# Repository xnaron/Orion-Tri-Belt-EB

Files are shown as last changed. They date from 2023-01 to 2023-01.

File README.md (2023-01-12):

# Orion Tri-Belt-EB

This is a fork of the awesome Orion bythorsthunder.  I wanted the electronics on the bottom.  

Changed CAD is in the EB-Mod folder.  I haven't exported any stl's.

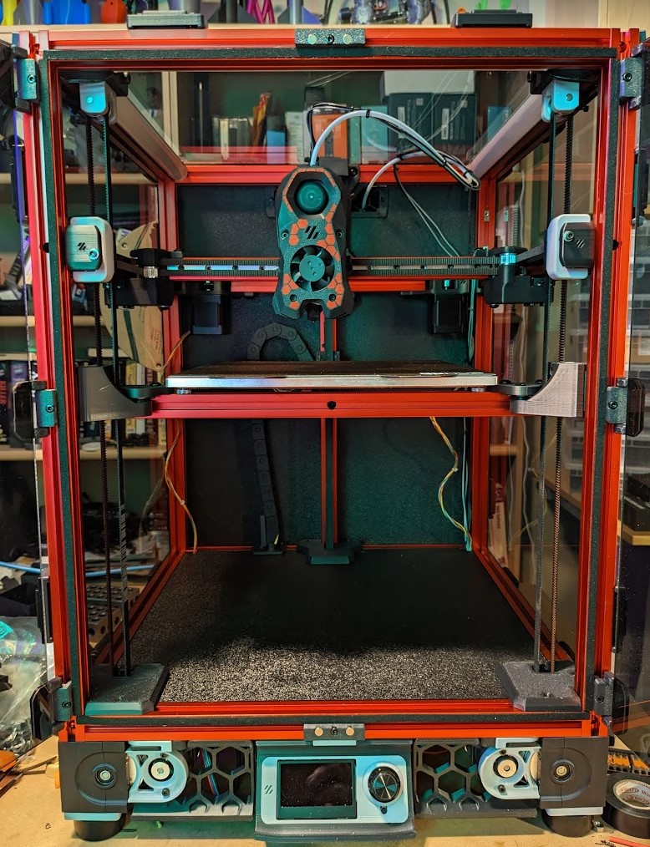
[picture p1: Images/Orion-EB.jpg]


A mod of the Voron Trident that replaces the 3 leadscrews with belts and modified Z-Drives from a 2.4.  This is in the very early stages of development and though a fully-functional printer has been built, some of the parts are not yet fully tested.  The existing printer is producing excellent prints, though many changes will be coming in the following months.

This first version places the Low Voltage Electronics up top, though I do hope to create a version in the future which is more closely matched to a stock Trident Build.  The second version will have the Z drives and low voltage electronics located on the bottom, same as in a standard Voron Trident or 2.4.

A huge thank you to [@clee](//github.com/clee/) for lots of help in planning, designing and generally supporting the development of this 3Dprinter.

## Why?

Since this is the most common question when posting about this printer, I will get this out of the way.  

  1. Much higher Z speeds and accelerations when compared to lead screws.  Tested so far at 200mm/s and 1000mm/s^2 without issues.
  2. Avoids the usual drawbacks of leadscrews regarding wobble and backlash.
  3. Similar cost to a Trident with lead screws, given the relatively high cost of steppers with integrated lead screws.
  4. Why not?

The cost of this modification is approximately $145 USD.  If the 3 steppers with lead screws are not purchased, the cost over a stock Trident build is approximately $40 USD.

## CAD

Due to max size for files on GitHub, [the CAD file can be downloaded from Dropbox](https://www.dropbox.com/s/zwozwpm1h77wviw/Orion%20Tri-Belt%20v5.step?dl=0).  There is a greatly trimmed-down file available in the CAD folder, but this link contains the most up to date full model.  

## BOM

The following is a list of parts required in addition to the stock Trident Build.

### Electronics

| Item | Qty |
| - | - |
| NEMA 17 stepper motor	| 3

### Motion	

| Item | Qty |
| - | - |
| 6mmx188mm GT2 Belt Loop | 3 |
|9MM 2GT Belt (Meters)	| 3.5
|Pulley 2GT 16 Tooth, 6mm	|  3
|Pulley 2GT 80 Tooth, 6mm	|  3
|Pulley 2GT 20 Tooth, 9mm	|  3
|Idler 2GT 20 Tooth, 9mm	|  3
|5x60 D-Shaft	|  3
|Bearing 625-2RS	|  9

### Fastners	
Buy extras.
| Item | Qty |
| - | - |
|M5x30 BHCS	|  3
|M5x10 BHCS	|  12+
|M5x40 SHCS	|  6
|M3x16 SHCS	|  3
|M3x40 SHCS	|  18
|M3 Heatsets	|  20
|M3x8 SHCS | Yes

## STLs
Print all files in the STLs folder.  Review readme.md in the Skirts folder for additional information.
For a new build skip the following when printing parts from the Trident repo.
### Excluded Parts
|Z_Assembly|Skirt|Panels|Gantry|
| - | - | - | - |
|[a]_z_carriage...|12864 Parts|bottom_panel...|Front Idlers|
|z_bed...|
|z_carriage...|
|z_stepper...|

### Additional Parts
From the Voron 2.4 Skirts Repo print the following:
| - |
|[a]_belt_guard
|[a]_fan_grill
|[a]_fan_grill_retainer
side_fan_support
side_skirt_a and b (Print only one of each)

## Panels
Upper deck panel can be created from the bottom panel.  DXF is included.

Deck Panel remains the same.

Rear Panel may benefit from some cutouts below the gantry extrusion to allow easier routing of wires from below deck to above.

Top LV electronics panel is a square with the same outside dimensions as the bottom panel.

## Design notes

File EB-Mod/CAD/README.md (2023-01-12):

2040 is used as a support in the back for rear idler.  See pics.  

To make the left and right z drive and idler just mirror them in the slicer.

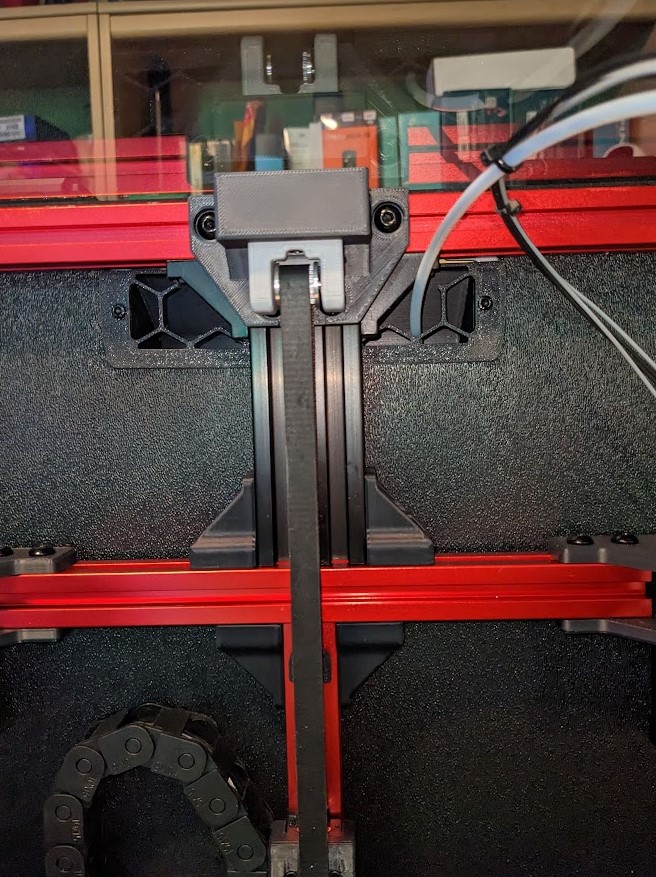
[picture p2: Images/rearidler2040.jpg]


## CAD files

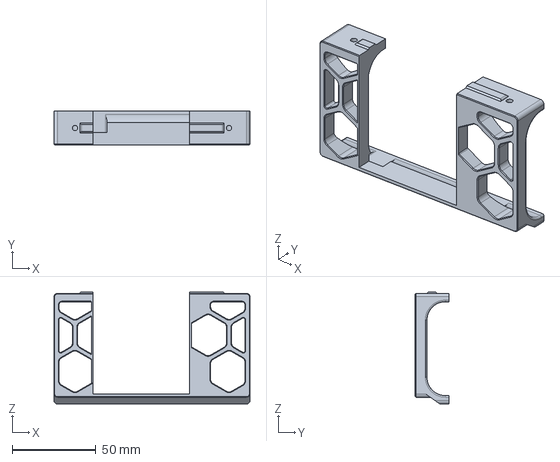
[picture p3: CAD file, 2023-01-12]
EB-Mod/CAD/250CenterRear v2.step
117.0 x 20.0 x 66.8 mm

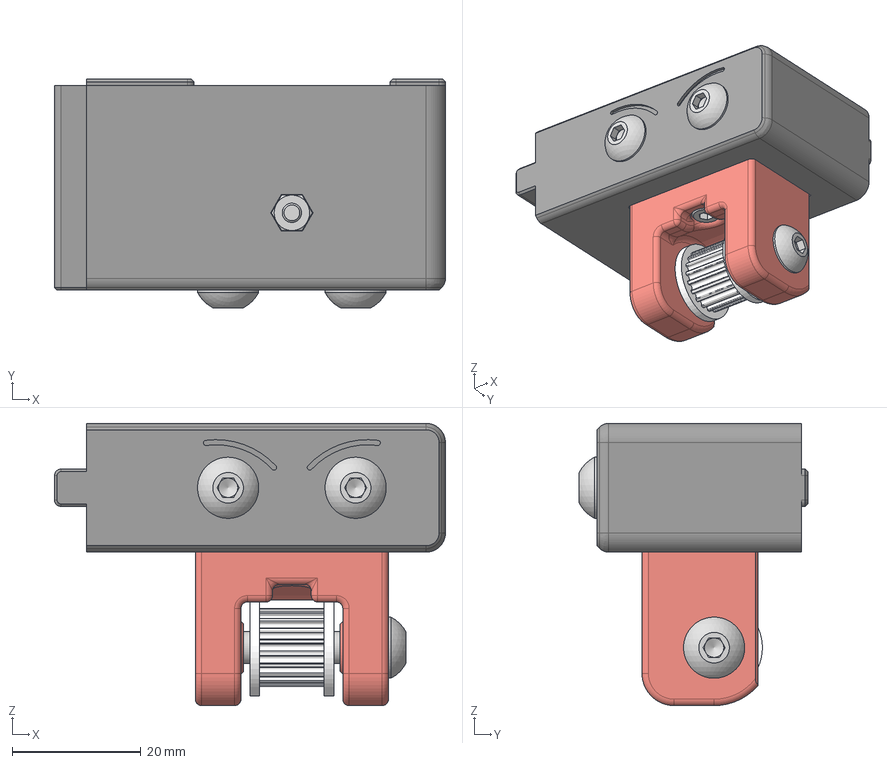
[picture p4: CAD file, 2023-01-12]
EB-Mod/CAD/Z Idler A v2.step
60.7 x 35.5 x 43.8 mm
GT2 20T Idler Gates 9mm
M5x30 BHCS (20)
M5x30 BHCS (10)
M5x30 BHCS (11)
M3 Hex Nut (2)
M3x16 SHCS (15)

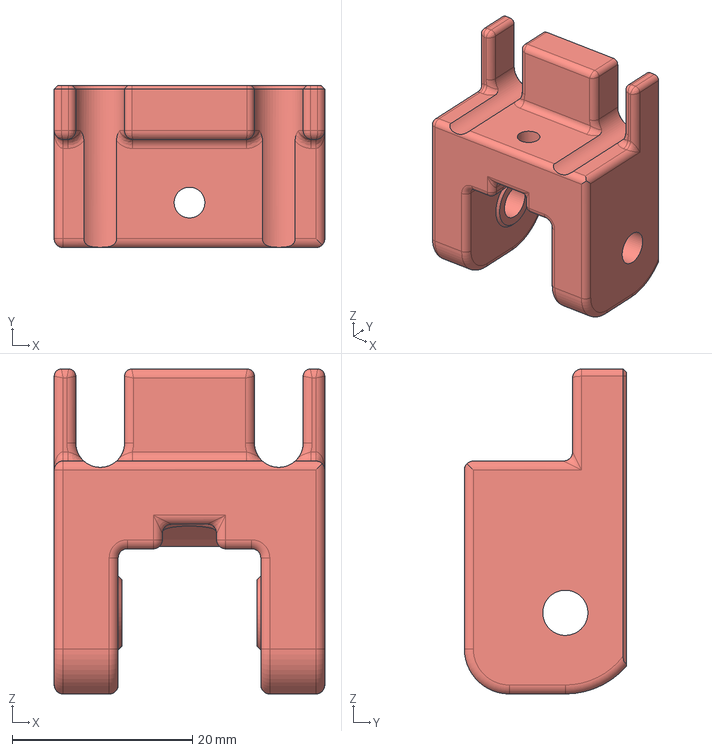
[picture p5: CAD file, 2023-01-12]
EB-Mod/CAD/Z Idler Rear 2040 v2.step
30.0 x 18.0 x 36.0 mm
